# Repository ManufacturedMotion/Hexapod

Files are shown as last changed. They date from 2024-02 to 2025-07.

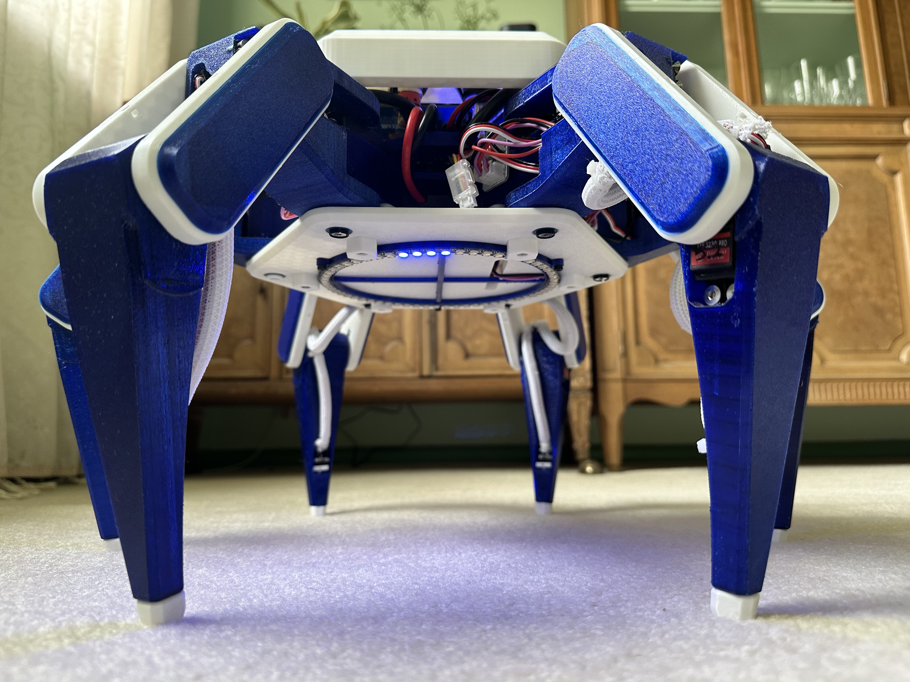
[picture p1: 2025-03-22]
resources/images/Hex2/dillon_bot_1.jpg

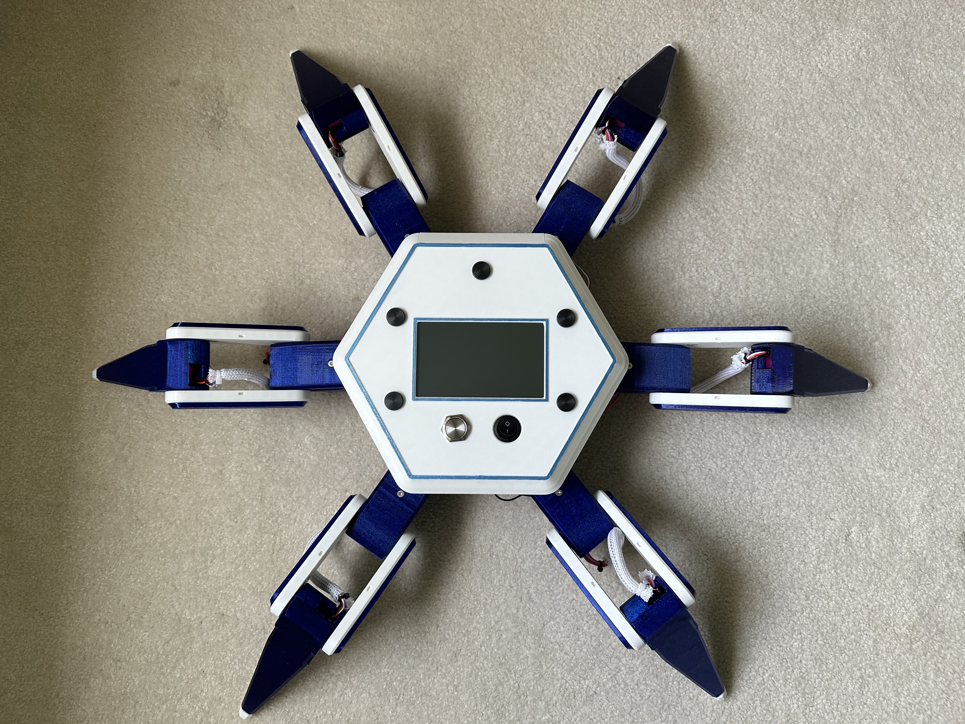
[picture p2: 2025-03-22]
resources/images/Hex2/dillon_bot_5.jpg

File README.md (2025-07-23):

# Hex

Hex is a six legged OpenSource Hexapod designed to serve as a moving platform for you to tinker with and build on top of! We are currently working on the third generation of the platform, Hex3.

If you're interested in learning more about the project, [visit our wiki!](https://github.com/ManufacturedMotion/Hexapod/wiki). If you want to build your own or join the community, check out our [Hex Discord](https://discord.gg/v3bbvRtFUr).

To find out info on what we're planning to change, [checkout our GitHub issues!](https://github.com/ManufacturedMotion/Hexapod/issues).

## Generations

### Hex1

- [Overview](https://github.com/ManufacturedMotion/Hexapod/wiki#mk1)
- Completed: July 2023 - May 2024
- MIT LICENSE

### Hex2
- [Overview](https://github.com/ManufacturedMotion/Hexapod/wiki#mk2)
- Completed: May 2024 - July 2025
- MIT LICENSE

### Hex3
- In-Progress: July 2025 - Present
- GNU GENERAL PUBLIC LICENSE V3

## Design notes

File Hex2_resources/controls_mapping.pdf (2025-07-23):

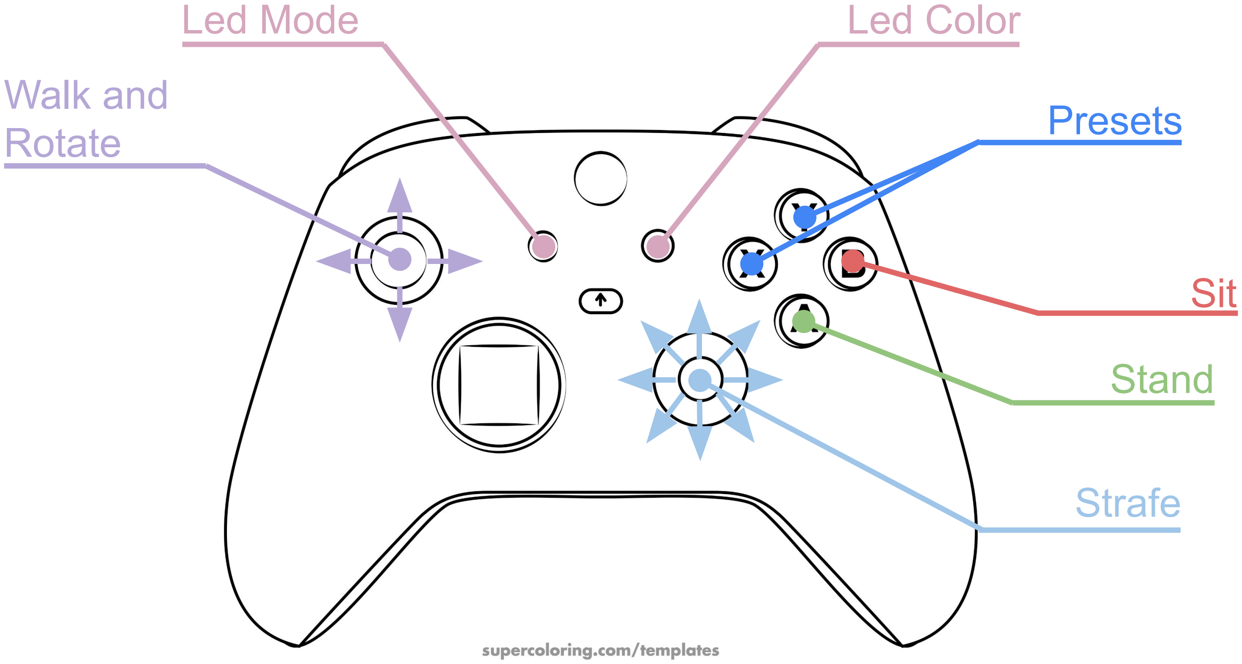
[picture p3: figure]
Walk and Rotate; Strafe; Led Mode; Led Color; Presets; Sit; Stand

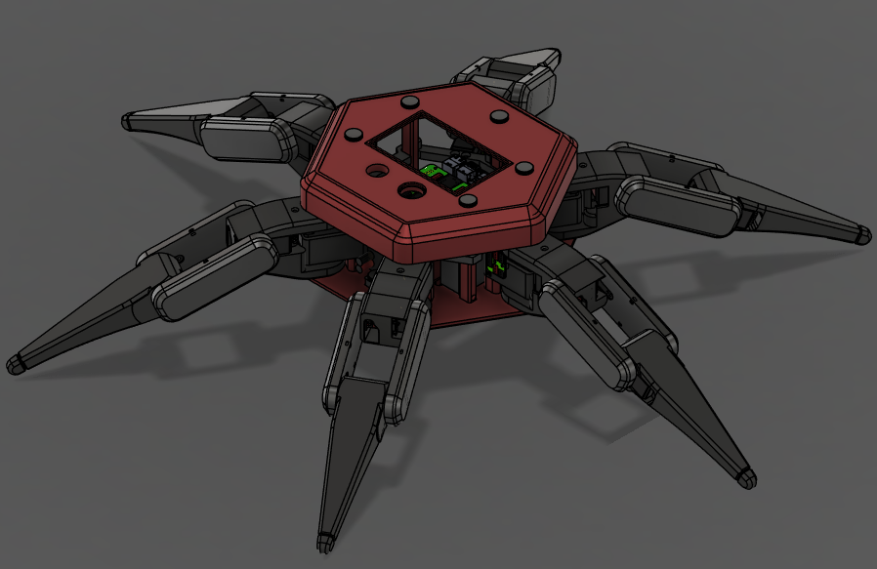
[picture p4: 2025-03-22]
resources/images/Hex2/cad.PNG

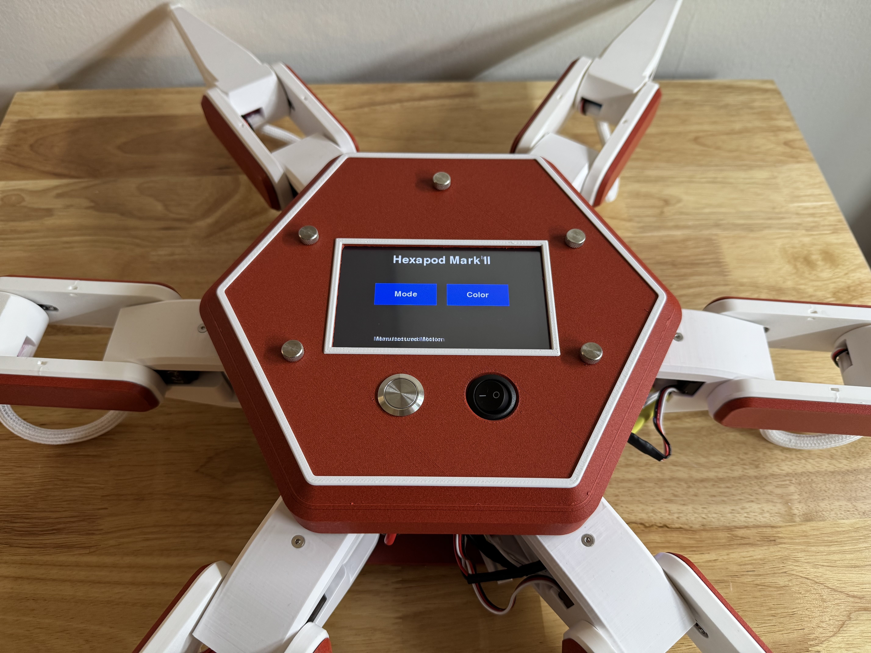
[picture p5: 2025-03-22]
resources/images/Hex2/danny_bot_3.jpg

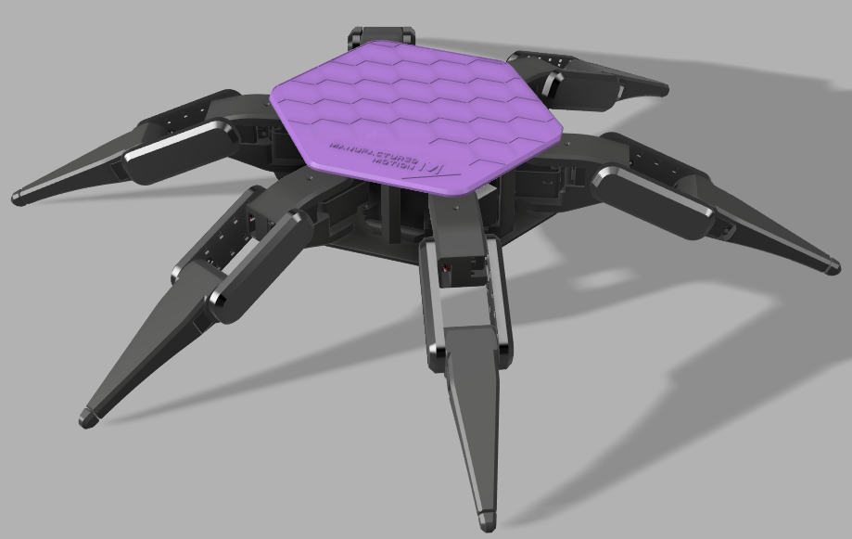
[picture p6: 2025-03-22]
resources/images/Hex1/cad_render.PNG

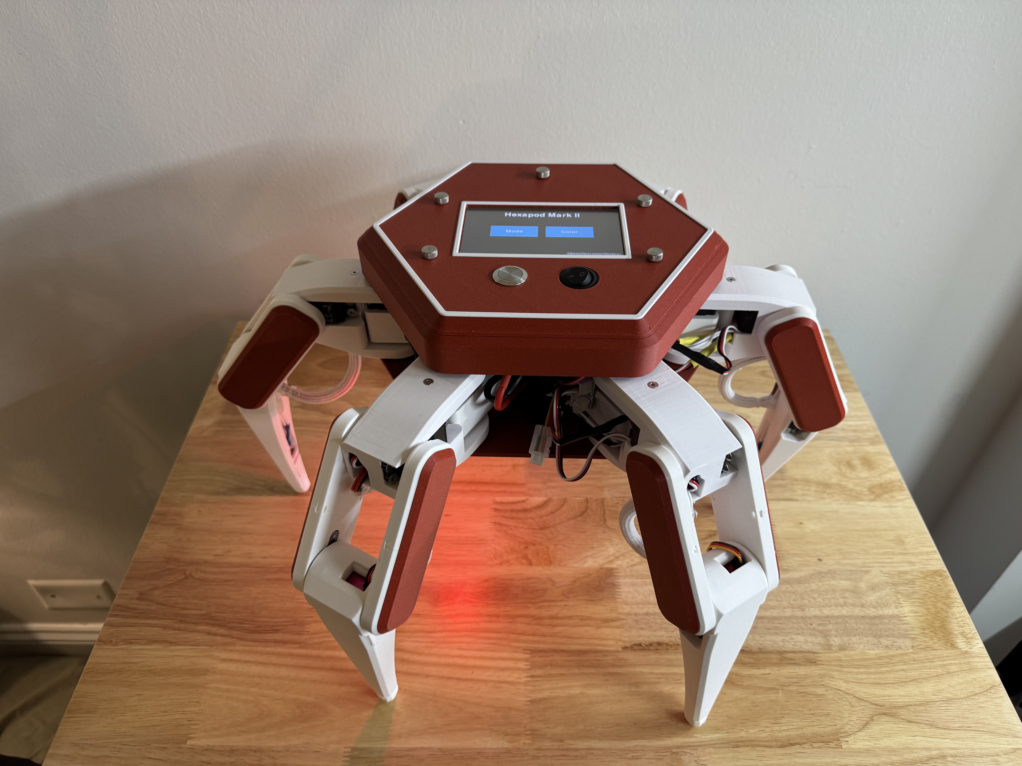
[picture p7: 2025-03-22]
resources/images/Hex2/danny_bot_4.jpg

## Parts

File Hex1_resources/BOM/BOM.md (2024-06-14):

# Bill of Materials

This BOM is non-exhaustive as we pivoted to developing the Hexapod Mk2, which is a more robust platform and solves a lot of the problems found in the Mk1 design. This includes a redesign of most of the 3D printed parts and electronics.

Please use the following parts as guidelines, rather than a definitive list.

## Printed Parts

The following files need to be 3D printed in order to assemble a Hexapod:

| Short Name  | Part Name/Description | Quantity | Notes |
|---|---|---|---|
| Base | Base Piece | 1 | |
| S1 | Segment 1 | 6 | |
| S2 | Segment 2 | 12 | Same part for left and right side |
| S2 Cover | Segment 2 Cover | 12 | Magnetically attached cover for S2 - Decorative Only |
| S3 | Segment 3 | 6 | |
| S3 Switch | Segment 3 Switch Cover | 6 | |
| S3 Mounting | Segment 3 Mounting Extension | 6 | |

Recommended Print Settings:

- 0.2mm layer height
- 3 Vertical Walls
- 10% Triangle Infill

## Electronics

| Category | Part | Quantity |
|---|---|---|
| Electronics | PCB | 1 |
| Electronics | [DS3230Pro-270 Degree Servos](https://www.aliexpress.us/item/2251801756814911.html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) | 18 |
| Electronics | [0805 SMD LED](https://www.amazon.com/dp/B01CUGA8JO/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) | 1 |
| Electronics | [0805 Resistor (Value TBD)](https://www.amazon.com/dp/B08RYMY6XK/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) | 1 |
| Electronics | [SPST Power Switch](https://www.amazon.com/DaierTek-Rocker-Switch-Household-Appliances/dp/B07S1MV462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) | 1 |
| Electronics | [Micro Limit Switch](https://www.amazon.com/dp/B073TYWX86/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) | 6 |
| Electronics | [DC-DC Buck Converter -- 12V to 5V 10A](https://www.amazon.com/dp/B0B1PG4C22/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) | 1 |
| Electronics | [JST-SM](https://www.amazon.com/gp/product/B071HFPXBD/ref=ppx_yo_dt_b_asin_title_o07_s00?ie=UTF8&psc=1) | 18 |
| Electronics | [JST-XH](https://www.amazon.com/gp/product/B07ZK5F8HP/ref=ppx_yo_dt_b_asin_title_o07_s00?ie=UTF8&psc=1) | 6 |
| Electronics | [XT60 PW](https://www.amazon.com/dp/B07VRLQ2C5?psc=1&ref=ppx_yo2ov_dt_b_product_details) | 1 |
| Electronics | [XT30 PW](https://www.amazon.com/dp/B099F2PXYN?psc=1&ref=ppx_yo2ov_dt_b_product_details) | 2 |
| Electronics | [XT30](https://www.amazon.com/dp/B08P5HVMYT?psc=1&ref=ppx_yo2ov_dt_b_product_details) | 2 |
| Electronics | [3s 5200 mAh Battery](https://www.amazon.com/dp/B0972RKJDS/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) | 1 |
| Electronics - Optional | [LiPo Battery Meter](https://www.amazon.com/dp/B0178P8H9U/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) | 1 |
| Electronics | [LiPo Charger](https://www.amazon.com/dp/B00466PKE0/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) | 1 |
| Electronics | [LiPo Charging Bag](https://www.amazon.com/dp/B07KZQZBN2/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) | 1 |
| Electronics | [Bluetooth Gaming Controller](https://www.amazon.com/dp/B0BFQFW9RS/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) | 1 |
| Electronics | [Teensy 4.0](http://d.digikey.com/dc/mn-w0iJh4uEE_bUitNCuXmOASUNxIUHHNt2ANEnMXZ9KmF9gFGcTP6LV0h4vvHht-UX6JWhwD_CEVqRHjYcqVHXxxIfGmGv3GtgizzJ-nkg94oIf-knrnSVyE2xlCqi3eC3-Q9X4k8dmw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) | 1 |
| Electronics | [Raspberry Pi Zero W](https://www.raspberrypi.com/products/raspberry-pi-zero-w/) | 1 |
| Electronics | [20 Awg Silicone Stranded Wire](https://www.amazon.com/dp/B06Y58W228?ref_=cm_sw_r_apin_dp_QD4W8PBN2DN0YP82QZBG&language=en-US&th=1) | TBD |

## Hardware

| Category | Part | Quantity |
|---|---|---|
| Hardware | [M4 x 4.7 Threaded Inserts](https://www.amazon.com/dp/B08T9TXS9S/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) | 72 |
| Hardware | [M3 x 5 Threaded Inserts](https://www.amazon.com/dp/B0CDH36ZMX/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) | 24 |
| Hardware | [6mm x 2mm Magnets](https://www.amazon.com/dp/B0C3B483DV/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) | 48 |
| Hardware | [ID 8mm x OD 14mm x Width 4mm Bearings](https://www.amazon.com/dp/B0C74VQDMM/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) | 12 |
| Hardware | [Hex Drive Flat Head Screw](https://www.mcmaster.com/#92125A190) [M4 x 0.7 mm Thread, 10 mm Long](https://www.mcmaster.com/#92125A190) | 72 |
| Hardware | [Hex Drive Flat Head Screw](https://www.mcmaster.com/#92125A130)[M3 x 0.5 mm Thread, 10 mm Long](https://www.mcmaster.com/#92125A130) | 60 |
| Hardware | [Cup-Point Set Screw](https://www.mcmaster.com/#91390A098)[M3 x 0.5 mm Thread, 4 mm Long](https://www.mcmaster.com/#91390A098) | 6 |
| Hardware | [Dowel Pin](https://www.mcmaster.com/#91585A573)[5 mm Diameter, 40 mm Long](https://www.mcmaster.com/#91585A573) | 6 |
| Hardware | [M2x10 Self Tap Screws](https://a.co/d/agRSm9J) | 12 |

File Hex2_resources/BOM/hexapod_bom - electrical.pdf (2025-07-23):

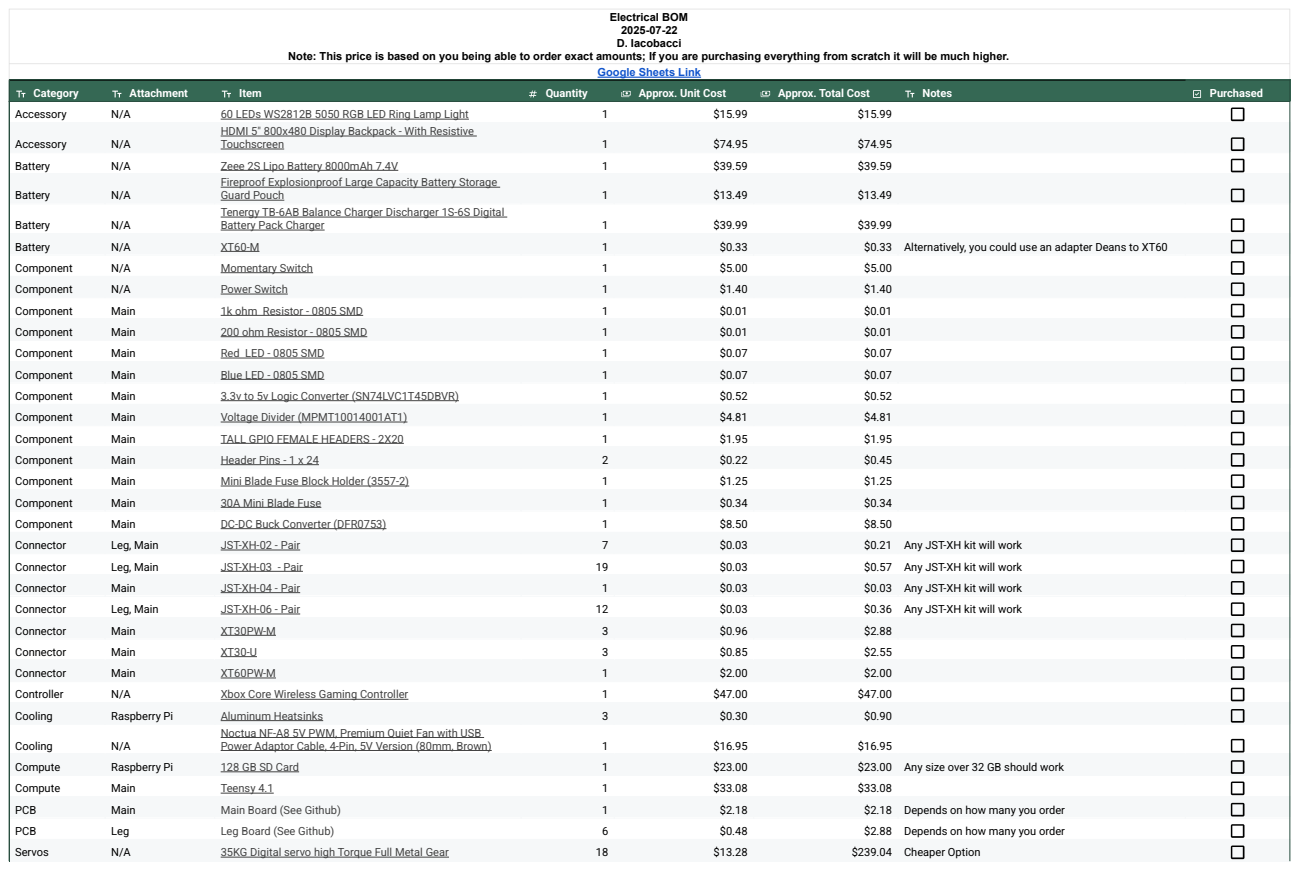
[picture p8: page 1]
Electrical BOM 2025-07-22 D. Iacobacci

Note: This price is based on you being able to order exact amounts; If you are purchasing everything from scratch it will be much higher.

Google Sheets Link (https://docs.google.com/spreadsheets/d/1nSNH1yMX1RCnKzeOJ6oc8cjoijGXfABLivroaHwzo4E/edit?usp=sharing)

Category | Attachment | Item | Quantity | Approx. Unit Cost | Approx. Total Cost | Notes | Purchased
Accessory | N/A | 60 LEDs WS2812B 5050 RGB LED Ring Lamp Light (https://www.amazon.com/dp/B083W2ZWTQ?ref_=ppx_hzsearch_conn_dt_b_fed_asin_title_1&th=1) | 1 | $15.99 | $15.99
Accessory | N/A | HDMI 5" 800x480 Display Backpack - With Resistive Touchscreen (https://www.adafruit.com/product/2260) | 1 | $74.95 | $74.95

Battery | N/A | Zeee 2S Lipo Battery 8000mAh 7.4V (https://www.amazon.com/dp/B073S2W6PZ/?coliid=I2N19MYR3S8E68&colid=2MOGJRAIUFLT0) | 1 | $39.59 | $39.59
Battery | N/A | Fireproof Explosionproof Large Capacity Battery Storage Guard Pouch (https://a.co/d/0e39bDe3) | 1 | $13.49 | $13.49

Battery | N/A | Tenergy TB-6AB Balance Charger Discharger 1S-6S Digital Battery Pack Charger (https://a.co/d/04OFANOm) | 1 | $39.99 | $39.99

Battery | N/A | XT60-M (https://www.amazon.com/dp/B07VRZR5TL?ref_=ppx_hzsearch_conn_dt_b_fed_asin_title_2) | 1 | $0.33 | $0.33 | Alternatively, you could use an adapter Deans to XT60

Component | N/A | Momentary Switch (https://a.co/d/0b9twNSM) | 1 | $5.00 | $5.00

Component | N/A | Power Switch (https://a.co/d/0cDl28JW) | 1 | $1.40 | $1.40

Component | Main | 1k ohm Resistor - 0805 SMD (https://a.co/d/05essy1o) | 1 | $0.01 | $0.01

Component | Main | 200 ohm Resistor - 0805 SMD (https://a.co/d/05essy1o) | 1 | $0.01 | $0.01

Component | Main | Red LED - 0805 SMD | 1 | $0.07 | $0.07

Component | Main | Blue LED - 0805 SMD (https://a.co/d/07H2SZfK) | 1 | $0.07 | $0.07

Component | Main | 3.3v to 5v Logic Converter (SN74LVC1T45DBVR) (https://www.digikey.com/en/products/detail/texas-instruments/SN74LVC1T45DBVR/639455) | 1 | $0.52 | $0.52

Component | Main | Voltage Divider (MPMT10014001AT1) (https://www.digikey.com/en/products/detail/vishay-dale-thin-film/MPMT10014001AT1/1771066) | 1 | $4.81 | $4.81

Component | Main | TALL GPIO FEMALE HEADERS - 2X20 (https://www.digikey.com/en/products/detail/sparkfun-electronics/PRT-21570/18635154) | 1 | $1.95 | $1.95

Component | Main | Header Pins - 1 x 24 (https://www.amazon.com/dp/B0CTKF2NC6/?coliid=I3O1AXN49NW8LT&colid=2MOGJRAIUFLT0) | 2 | $0.22 | $0.45

Component | Main | Mini Blade Fuse Block Holder (3557-2) (https://www.digikey.com/en/products/detail/keystone-electronics/3557-2/2137305) | 1 | $1.25 | $1.25

Component | Main | 30A Mini Blade Fuse (https://www.digikey.com/en/products/detail/littelfuse-inc/0891030-NXWS/5233823) | 1 | $0.34 | $0.34

Component | Main | DC-DC Buck Converter (DFR0753) (https://www.digikey.com/en/products/detail/dfrobot/DFR0753/13590872) | 1 | $8.50 | $8.50

Connector | Leg, Main | JST-XH-02 - Pair (https://a.co/d/03VvZ2aq) | 7 | $0.03 | $0.21 | Any JST-XH kit will work

Connector | Leg, Main | JST-XH-03 - Pair (https://a.co/d/03VvZ2aq) | 19 | $0.03 | $0.57 | Any JST-XH kit will work

Connector | Main | JST-XH-04 - Pair (https://a.co/d/03VvZ2aq) | 1 | $0.03 | $0.03 | Any JST-XH kit will work

Connector | Leg, Main | JST-XH-06 - Pair (https://a.co/d/03VvZ2aq) | 12 | $0.03 | $0.36 | Any JST-XH kit will work

Connector | Main | XT30PW-M (https://a.co/d/0aSlfwzo) | 3 | $0.96 | $2.88

Connector | Main | XT30-U (https://a.co/d/017gKTzp) | 3 | $0.85 | $2.55

Connector | Main | XT60PW-M (https://a.co/d/06amuL7W) | 1 | $2.00 | $2.00

Controller | N/A | Xbox Core Wireless Gaming Controller (https://a.co/d/02mnp9V5) | 1 | $47.00 | $47.00

Cooling | Raspberry Pi | Aluminum Heatsinks (https://a.co/d/04IbYiWU) | 3 | $0.30 | $0.90
Cooling | N/A | Noctua NF-A8 5V PWM, Premium Quiet Fan with USB Power Adaptor Cable, 4-Pin, 5V Version (80mm, Brown) (https://a.co/d/0ccSLfRo) | 1 | $16.95 | $16.95

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

Electrical BOM
2025-07-22
D. Iacobacci
Note: This price is based on you being able to order exact amounts; If you are purchasing everything from scratch it will be much higher. Google Sheets Link (https://docs.google.com/spreadsheets/d/1nSNH1yMX1RCnKzeOJ6oc8cjoijGXfABLivroaHwzo4E/edit?usp=sharing)
Category | Attachment | Item | Quantity | Approx. Unit Cost | Approx. Total Cost | Notes | Purchased
Servos | N/A | GoBilda 2000 Series Dual Mode Servo (25-2, Torque) | 18 | $31.44 | $565.92 | Price includes 15% bulk discount if you order 20 or more -- email GoBilda directly.
Compute | Raspberry Pi | Raspberry Pi 5 - 8 GB RAM (https://www.adafruit.com/product/5813) | 1 | $80.00 | $80.00
Wiring | N/A | Micro HDMI to HDMI Wire A2-D2 (https://www.aliexpress.us/item/3256802017399860.html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) | 0 | $2.35 | $0.00 | Confirm orientation works for your screen and pi
Wiring | N/A | Main to Leg Connections <TBD> | 0 | $ -
Wiring | N/A | 12 Gauge Wire (https://www.amazon.com/dp/B07CZZ11K2/?coliid=I1EO3TKVNQHO26&colid=2MOGJRAIUFLT0) | 1 | $0.66 | $0.66 | Used for the power switch as it has the full battery current; Could likely go with a lower gauge
| | | | $0.66 | $0.00
| | | | $0.66 | $0.00
| | | | | $663.01 | Price with AliExpress servos
| | | | | $989.89 | Price with GoBilda servos

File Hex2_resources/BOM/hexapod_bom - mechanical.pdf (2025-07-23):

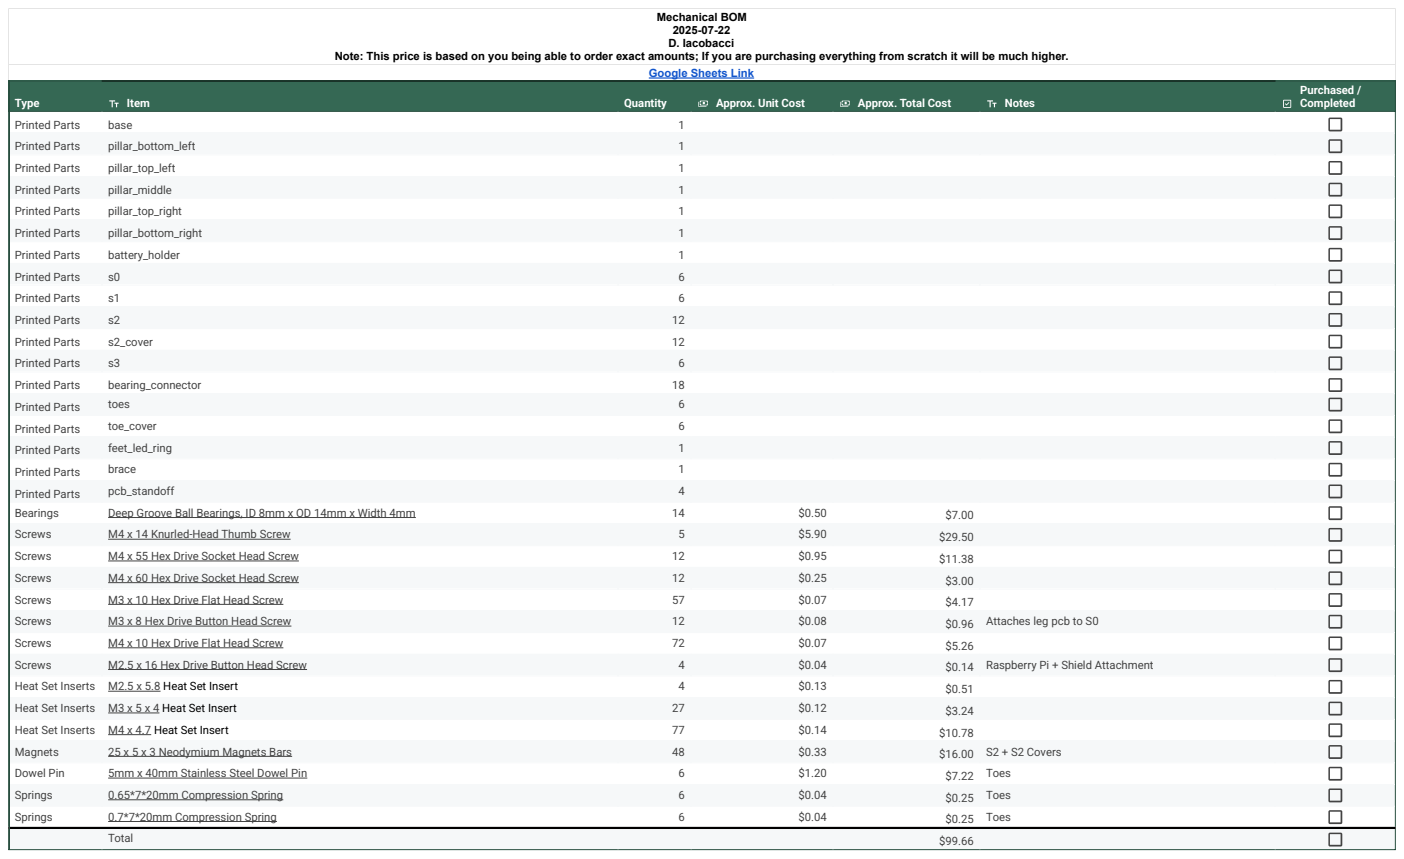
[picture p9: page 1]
Mechanical BOM 2025-07-22 D. Iacobacci

Note: This price is based on you being able to order exact amounts; If you are purchasing everything from scratch it will be much higher.

Google Sheets Link (https://docs.google.com/spreadsheets/d/1nSNH1yMX1RCnKzeOJ6oc8cjoijGXfABLivroaHwzo4E/edit?usp=sharing)

Type | Item | Quantity | Approx. Unit Cost | Approx. Total Cost | Notes | Purchased / Completed

Printed Parts | base | 1

Printed Parts | pillar_bottom_left | 1

Printed Parts | pillar_top_left | 1

Printed Parts | pillar_middle | 1

Printed Parts | pillar_top_right | 1

Printed Parts | pillar_bottom_right | 1

Printed Parts | battery_holder | 1

Printed Parts | s0 | 6

Printed Parts | s1 | 6

Printed Parts | s2 | 12

Printed Parts | s2_cover | 12

Printed Parts | s3 | 6

Printed Parts | bearing_connector | 18
Printed Parts | toes | 6

Printed Parts | toe_cover | 6

Printed Parts | feet_led_ring | 1

Printed Parts | brace | 1

Printed Parts | pcb_standoff | 4

Bearings | Deep Groove Ball Bearings, ID 8mm x OD 14mm x Width 4mm (https://www.amazon.com/gp/product/B0C74VQDMM/ref=ppx_yo_dt_b_search_asin_title?ie=UTF8&th=1) | 14 | $0.50 | $7.00

Screws | M4 x 14 Knurled-Head Thumb Screw (https://www.mcmaster.com/92545a155/) | 5 | $5.90 | $29.50

Screws | M4 x 55 Hex Drive Socket Head Screw (https://www.mcmaster.com/catalog/91292A268) | 12 | $0.95 | $11.38

Screws | M4 x 60 Hex Drive Socket Head Screw | 12 | $0.25 | $3.00

Screws | M3 x 10 Hex Drive Flat Head Screw (https://www.mcmaster.com/catalog/92125A130) | 57 | $0.07 | $4.17

Screws | M3 x 8 Hex Drive Button Head Screw (https://www.mcmaster.com/92095A181) | 12 | $0.08 | $0.96 | Attaches leg pcb to S0

Screws | M4 x 10 Hex Drive Flat Head Screw (https://www.mcmaster.com/92125A130/) | 72 | $0.07 | $5.26

Screws | M2.5 x 16 Hex Drive Button Head Screw (https://www.amazon.com/gp/product/B09CPDVYB7/ref=ppx_yo_dt_b_search_asin_title?ie=UTF8&psc=1) | 4 | $0.04 | $0.14 | Raspberry Pi + Shield Attachment

Heat Set Inserts | M2.5 x 5.8 Heat Set Insert | 4 | $0.13 | $0.51

Heat Set Inserts | M3 x 5 x 4 Heat Set Insert | 27 | $0.12 | $3.24

Heat Set Inserts | M4 x 4.7 Heat Set Insert | 77 | $0.14 | $10.78

Magnets | 25 x 5 x 3 Neodymium Magnets Bars (https://www.amazon.com/gp/product/B09YCWKBMP/ref=ppx_yo_dt_b_search_asin_title?ie=UTF8&th=1) | 48 | $0.33 | $16.00 | S2 + S2 Covers

Dowel Pin | 5mm x 40mm Stainless Steel Dowel Pin (https://www.mcmaster.com/91585A573/) | 6 | $1.20 | $7.22 | Toes

Springs | 0.65*7*20mm Compression Spring (https://www.amazon.com/dp/B0BBQL2SN3?ref_=ppx_hzsearch_conn_dt_b_fed_asin_title_3) | 6 | $0.04 | $0.25 | Toes

Springs | 0.7*7*20mm Compression Spring (https://www.amazon.com/dp/B0BBQL2SN3?ref_=ppx_hzsearch_conn_dt_b_fed_asin_title_3) | 6 | $0.04 | $0.25 | Toes

Total | | | $99.66

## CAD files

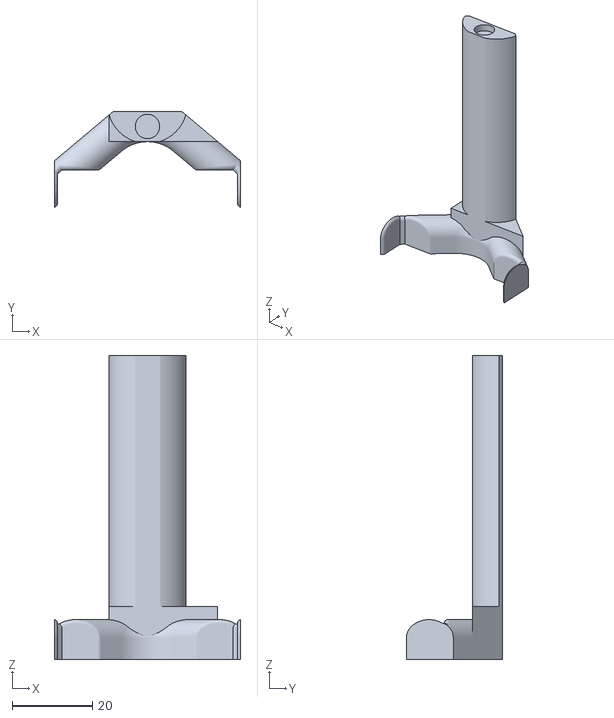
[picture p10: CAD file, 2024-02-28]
Hex1_resources/CAD/base_batteryholder_final.stl
46.5 x 24.0 x 76.0

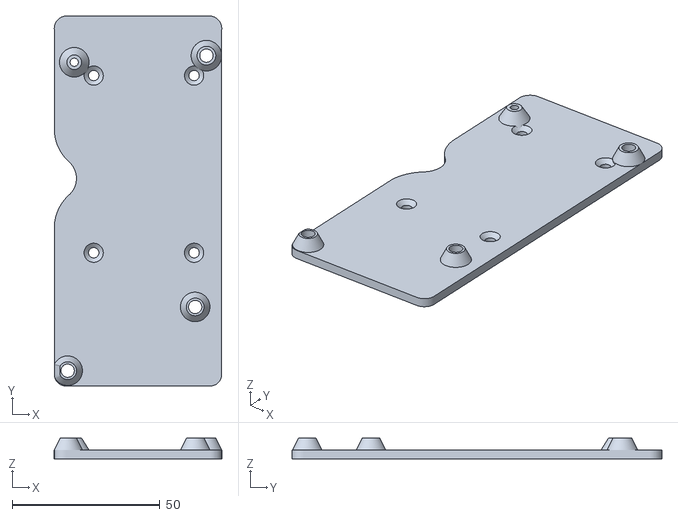
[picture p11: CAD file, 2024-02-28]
Hex1_resources/CAD/pcb_mount_final.stl
56.7 x 125.3 x 7.00

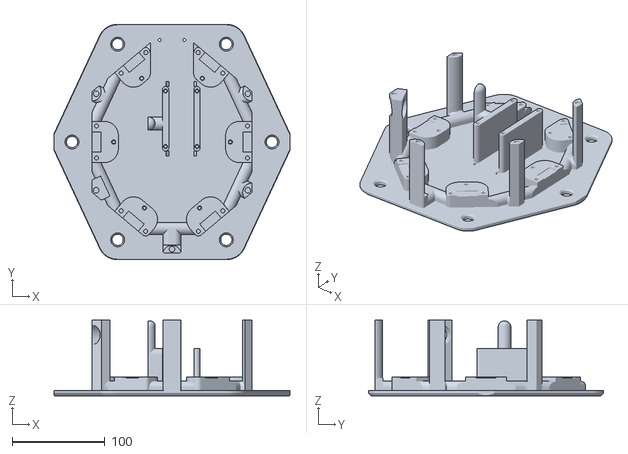
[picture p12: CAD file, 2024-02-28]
Hex1_resources/CAD/base_bottom_final.stl
255.0 x 254.4 x 82.0

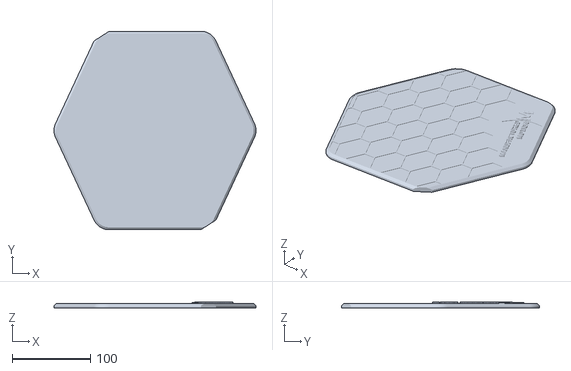
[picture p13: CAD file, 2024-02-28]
Hex1_resources/CAD/lid_wlogo_final.stl
259.0 x 254.4 x 8.00

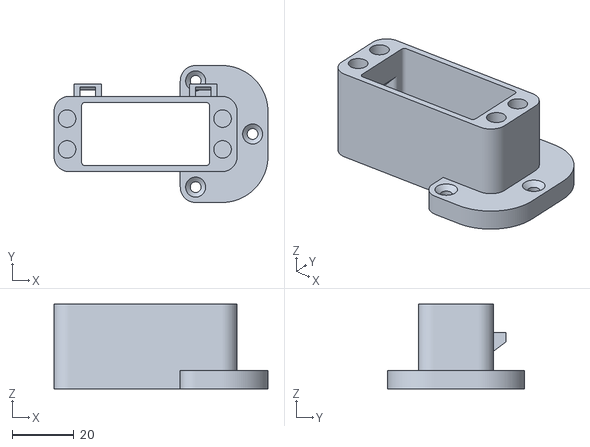
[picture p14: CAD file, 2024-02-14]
Hex1_resources/CAD/L2,3,4,5 - S1 Motor Mount - Final.stl
69.5 x 44.5 x 27.5

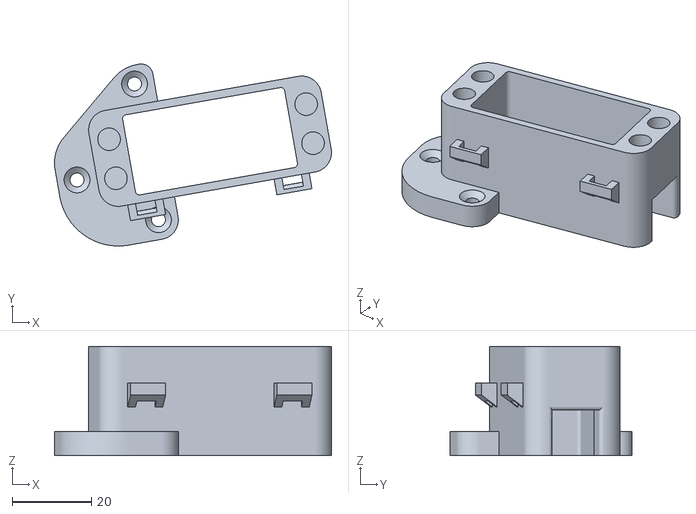
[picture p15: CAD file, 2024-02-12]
Hex1_resources/CAD/L2 - S1 Motor Mount - Final.stl
69.9 x 45.9 x 27.5

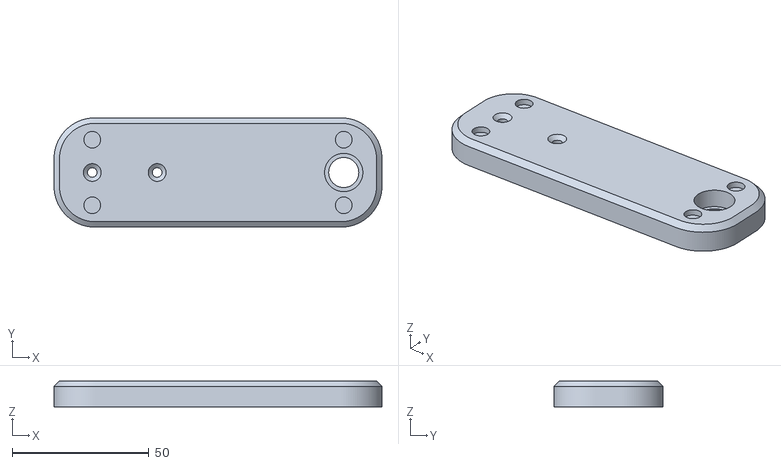
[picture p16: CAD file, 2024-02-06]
Hex1_resources/CAD/S2 Final.stl
120.0 x 40.0 x 9.50

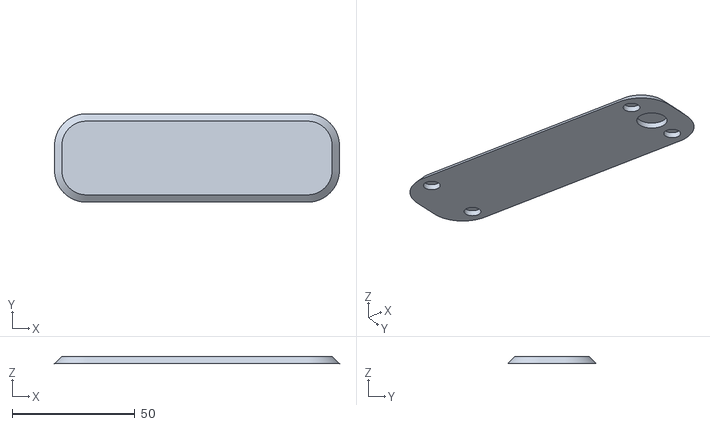
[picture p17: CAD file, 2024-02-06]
Hex1_resources/CAD/S2 Cover Final.stl
116.0 x 36.0 x 3.00

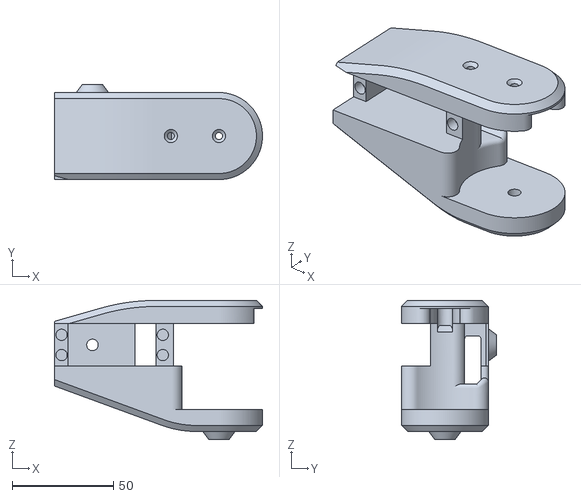
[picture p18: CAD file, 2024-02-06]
Hex1_resources/CAD/S1 Final.stl
102.8 x 47.0 x 68.8

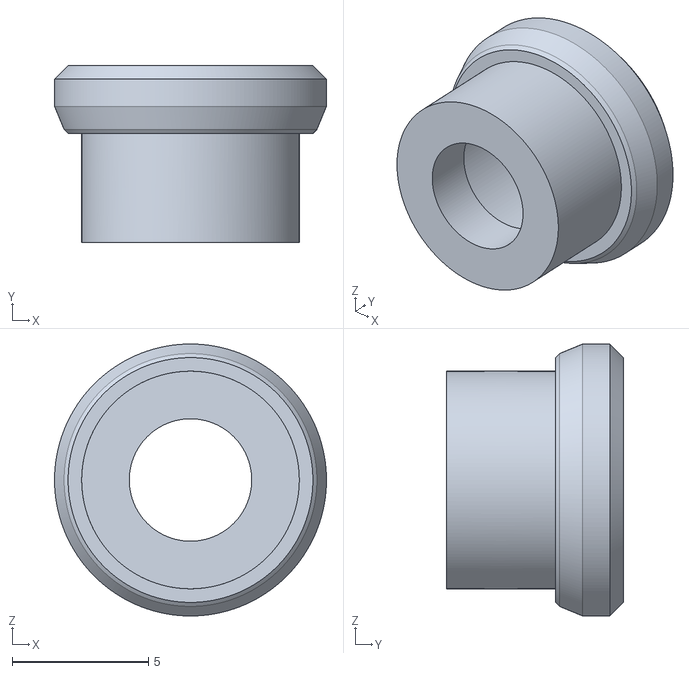
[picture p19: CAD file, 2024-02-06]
Hex1_resources/CAD/Bearing Holder.stl
10.0 x 6.50 x 10.00

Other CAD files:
Hex1_resources/CAD/L6 - S1 Motor Mount - Final.stl

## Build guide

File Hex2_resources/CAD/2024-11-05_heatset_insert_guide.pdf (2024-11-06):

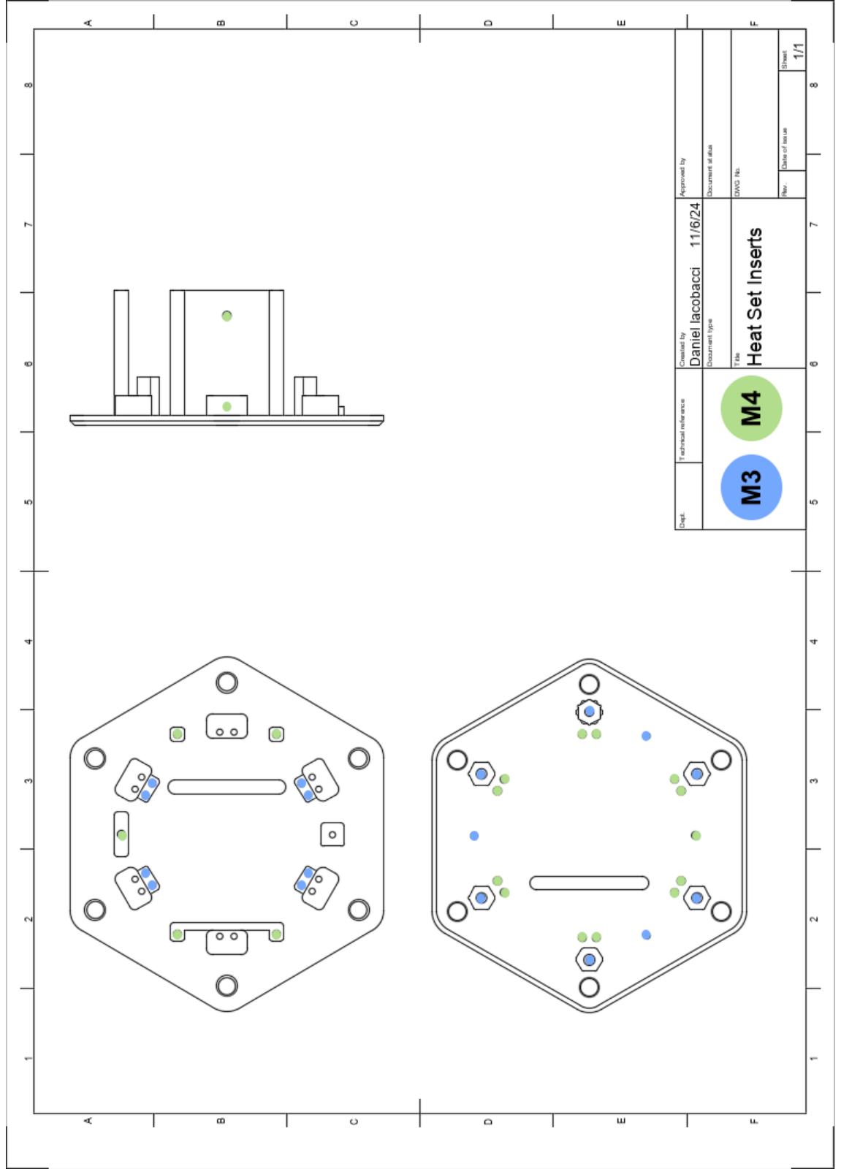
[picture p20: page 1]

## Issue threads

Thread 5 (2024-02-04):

Header File with Configuration

Diacoba1, 2024-02-04:
Write code that takes in an offsets.h file and can use each of our offsets in the code. Should be flexible enough that we just need to specify whose bot it is, and the rest is abstracted away.

DillonKane, 2024-02-05:
First rev done. Could not dynamically create an array of axis objects and then use a for loop to define motor pins, etc. Instead that is hard coded for now -- this was what I was trying:

```
Axis axes[6][3];
  for (uint8_t i = 0; i < 6; i++) {
    for (uint8_t j = 0; j < 3; j++) {
        axes[i][j] = Axis(pwm_pins[i][j], min_pos[i][j] * scale_fact[i][j], max_pos[i][j] * scale_fact[i][j]);
    }
  }
```
This was not correctly meshing with the servos

Diacoba1, 2024-02-29:
- [ ] PWM pins defined per user
- [ ] Swap zero points for L1 & L2 for Danny and Zack
- [ ] Move `#define USER DILLON` to before the includes of the Arduino file

DillonKane, 2024-02-29:
https://github.com/ManufacturedMotion/HexapodController/pull/2

Closed 2024-02-29.

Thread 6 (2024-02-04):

Update the Base to allow for Battery removal

Diacoba1, 2024-02-04:
Modify the base to allow the battery to be slid in and out on the side with the custom fit brackets. It should be held in place with the lid mounting piece that has two screws.

Diacoba1, 2024-02-06:
#10

Closed 2024-02-06.

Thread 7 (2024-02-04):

Update the S1 Mounting

Diacoba1, 2024-02-04:
Update the S1 Mounting to:

- Allow for 4 screws to be used
- Have the chamfer on the correct side
- Have the mounting screws in the correct place

Closed 2024-02-12.

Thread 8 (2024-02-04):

Position and Orientation of Robot

Diacoba1, 2024-02-04:
From ChatGPT:
I have a robot with three legs. With it standing on those three legs, I want it to calculate the position and orientation of the center of the robot. How can I do this?

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

Diacoba1, 2024-02-29:
Decided coordinate system, in progress. Need to figure out how Yaw impacts X and Y

Closed 2024-04-04.

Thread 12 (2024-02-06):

Update Servo Mounts

DillonKane, 2024-02-06:
update screw spacing on all servo mounts so all 4 screws can be used

Diacoba1, 2024-02-12:
Cleared assignees -- we should only assign to one person so we know who is tackling it

Diacoba1, 2024-02-12:
I have already updated S1, and S2. The final change needs to be done for S3. But we should lump it in with the toe fixes

Diacoba1, 2024-02-13:
- [ ] Update S1 Motor mount to not have an overhang
- [ ] Check out S3 spacing

Closed 2024-02-14.

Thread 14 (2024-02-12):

Update S3 Toe Mount

Diacoba1, 2024-02-12:
Update S3 so the toe rod is held in place, and the limit switch cover so we don't need to cut away parts of S3

Diacoba1, 2024-03-15:
Dillon test this

Closed 2024-03-28.

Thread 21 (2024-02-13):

Raspberry Pi Passthrough

Diacoba1, 2024-02-13:
- [ ] A pass through using serial to send commands to the Teensy
- [ ] SSH into the raspberry pi wirelessly, run a script that gives us a serial monitor

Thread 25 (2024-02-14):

Design the Lid

Diacoba1, 2024-02-14:
The lid should meet the following requirements:

- [x] Be able to be printed in two colors without the need of an AMS
- [x] Have the Manufactured Motion Logo Printed on the Lid
- [x] Securely attach to the base with as few screws as possible (max 6)
- [x] Attach with screws standard to the rest of the bot
- [x] Provide access to the switch
- [x] Cover cables without significantly increasing height or restricting range of motion

Closed 2024-02-28.

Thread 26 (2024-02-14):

Redesign S3

Diacoba1, 2024-02-14:
Redesign S3 to address the following issues/concerns:

- [x] The zip tie mounts in the cable channel do not function properly
- [x] The servo can only use 2/4 screws
- [x] The motor connector piece can easily be overtightened, cracking the piece
- [x] The part is not optimized for 3D printing -- significant supports are needed and they are hard to remove

Diacoba1, 2024-04-03:
Just need to upload the new files to Github

Closed 2024-04-14.

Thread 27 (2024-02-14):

PCB Second Generation

Diacoba1, 2024-02-14:
Making this issue to track future improvements to the PCB:

- [x] **Convert the PCB to working with a Raspberry Pi 5 instead of a Pi Zero W**
- [x] PCB should attach to the Raspberry Pi (breakout attachment)
- [x] Change the motor connector order so it goes 123 instead of 213
- [x] Change the switch connector to be an XT-30 instead of two vias
- [x] Improve the readability of the silkscreen once connectors are attached
- [x] ~Add in physical low voltage cutoff~ Dropping this in favor of a way to read the voltage and get those values on the pi.
- [x] ~Add in Touchscreen for current status~ USB + HDMI, no physical connections required
- [x] Lever to switch between control modes (redesign not required) (Or dipswitches on the board?)
- [x] ~Big button for regular and autonomous~ Deprecating in favor of the touch screen
- [x] ~1-3 LEDs for status indication~ Deprecating in favor of the touch screen
- [x] Add in the Manufactured Motion logo to the back of the PCB
- [x] ~Connections for Lidar~ -- should be USB

Diacoba1, 2024-06-04:
#83 Began working on some of these points

Diacoba1, 2024-06-25:
#97

Closed 2024-06-25.

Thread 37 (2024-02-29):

Measure from actual center of bot to S1 for each leg

Diacoba1, 2024-02-29:
Measure from actual center of bot to S1 for each leg. Get the X and Y offsets.

- With battery on the bottom, L/R is X, Up/Down is Y.
- Half the values should be negative

3 | 4
2 | 5
1 | 6

Diacoba1, 2024-03-09:
#45

Closed 2024-03-09.

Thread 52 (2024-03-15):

Update Example File

Diacoba1, 2024-03-15:
- [x] Case 0 is a break
- [x] Case 1-6 controls that specific legs IK
- [x] Case 7 move to all zeros
- [x] Each case should have its own scanf

Diacoba1, 2024-03-23:
https://github.com/ManufacturedMotion/HexapodController/pull/4

Closed 2024-03-23.

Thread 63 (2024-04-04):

WebServer Enhancements

Diacoba1, 2024-04-04:
- [x] Swap from Threads to multiprocessing (true multi-threading) on the Pi
- [x] Fix the read serial action so it is properly sent to the webpage

Diacoba1, 2024-04-04:
#65

Closed 2024-04-04.

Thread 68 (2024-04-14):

Raspberry Pi as a WAP

Diacoba1, 2024-04-14:
- [x] If there is a network available, use that network
- [x] If there is not, launch a soft-access point

Diacoba1, 2024-06-21:
A lot of these issues go away with the transition to a full pi running Ubuntu, so closing out

Closed 2024-06-21.

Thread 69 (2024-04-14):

Raspberry Pi WebServer does not function w/o hard access point

Diacoba1, 2024-04-14:
- [ ] Flask WebServer fails without an internet connection -- why?
- [ ] Logo is not rendered as it is hosted on Github

Diacoba1, 2024-06-25:
Not an issue with running Ubuntu, we can have it act as a bridge between the network and the user

Closed 2024-06-25.

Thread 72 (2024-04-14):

Leg Breakout Boards

Diacoba1, 2024-04-14:
Instead of needing each leg to have a wiring harness, we should design a small PCB to mount to each S0.

- [x] Connectors for the data for each servo
- [x] Common ground and 5v lines
- [x] Screw mounting

Diacoba1, 2024-06-21:
#88

Closed 2024-06-21.

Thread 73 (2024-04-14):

Hexapod Gen 2

Iacobacci, 2024-04-14:
- [x] **Redesign the hexapod base to function with the Gen 2 PCB**
- [x] Significantly larger magnets so the base could be lifted up from the magnets
- [x] Adjust the logo on the lid so it always is at the back of the hexapod
- [x] Modify S1 to be able to fit connectors through the cable routing hole

Iacobacci, 2024-08-22:
#107

Closed 2024-08-22.

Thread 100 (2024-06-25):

Test the mk2 main board

Iacobacci, 2024-06-25:
Confirm the following works:

- [x] Voltage divider outputs a voltage within the acceptable range for the pins
- [x] pi can control LED ring
- [x] pi can talk to teensy
- [x] pi can control fan
- [x] voltage divider sends correct value to teensy (battery reading)
- [x] new board can control servos

DillonKane, 2024-08-24:
can measure temp for fan control logic with "sudo vcgencmd measure_temp"

DillonKane, 2024-08-24:
voltage divider needs to be multiplied by offset of 0.01606 to get correct reading

DillonKane, 2024-08-31:
voltage divider sends vdd of 2.45 with battery vdd of 12.3V

zschwid, 2024-10-13:
Can we get a status update here?

DillonKane, 2024-11-19:
Pi can control LED ring if jumper connector is used for LED signal wire. Jumper connects SIG to Pi pin MOSI SCLK0.

Will be addressed with PCB redesign

Closed 2024-11-19.

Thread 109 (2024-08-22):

"Final" CAD Revisions

Iacobacci, 2024-08-22:
- [x] Update S2 Magnets
- [x] S3 Revisions
- [x] Modify lid to cover bot more
- [x] Expand buffer around battery
- [x] Tighter tolerance on brace
- [x] Chamfer brace corners
- [x] Make middle lid support wider
- [x] Cable management

Iacobacci, 2024-08-27:
#111

Closed 2024-08-27.

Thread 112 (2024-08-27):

Mechanical BOM

Iacobacci, 2024-08-27:
Put together a BOM of all the mechanical parts (3D printed parts, screws, bearings, magnets, etc) needed to assemble the hexapod

Iacobacci, 2025-01-20:
Rough draft done in #152 , closing out until project is complete

Closed 2025-01-20.

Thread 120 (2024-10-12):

Assess walking robot simulation frameworks

zschwid, 2024-10-12:
Determine a good framework to use for simulation of the hexapod for RL training

Iacobacci, 2025-02-14:
Switching from Gazebo to IsaacGym

Closed 2025-02-14.

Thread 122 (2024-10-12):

Model has inconsistencies with small motions

zschwid, 2024-10-12:
Very small steps can lead to commanding positions that the hexapod mechanically cannot keep up with. Rework model to account for this case

Closed 2025-02-14.

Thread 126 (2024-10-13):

Voltage drops momentarily when all motors make collision, causing the RPi to shutdown due to undervoltage

zschwid, 2024-10-13:
Fixes to try:
- Add bulk / decoupling capacitance
- Bigger buck converter

Iacobacci, 2024-11-14:
We are going to remediate this with a PCB re-design to run the servos independently off the battery, with the Buck converter being dedicated to the Pi, Fan, LEDs, and other peripherals. Tracked In #130

Closed 2024-11-14.

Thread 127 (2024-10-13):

CAD Changes

zschwid, 2024-10-13:
- [x] S0 PCB mounting
- [x] Bracket (Brace)
- [x] Lid fixes
- [x] Upload archive to git

Closed 2024-11-06.

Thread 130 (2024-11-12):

PCB Redesign

Iacobacci, 2024-11-12:
Redesign the PCB to isolate the servo power and the 5V regulated power.

Schematic:
- [x] Validate the servos can run directly off a 7.4v battery (and up to the maximum charge).
- [x] Run the servos off 7.4v (battery voltage) rather than 5v from the buck converter.
- [x] Add a replaceable fuse (40A) off the battery as a maximum draw.
- [x] ~Switch the Dip Switch to be through hole rather than surface mount.~ Remove the dip switches
- [x] Update Pi power switch to use Pins 9 and 11 (GND, GPIO 17)

Board:
- [x] New board layout
- [x] Order board via JLC/PCBway

Closed 2024-11-26.

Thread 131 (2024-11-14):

Raspberry Pi Soft Shutdown

Iacobacci, 2024-11-14:
The raspberry pi should trigger a soft shutdown when the appropriate button is pressed. This will prevent the SD card from corrupting, which is caused by improper shutdowns.

Closed 2024-11-24.

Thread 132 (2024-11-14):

Xbox Controller to Single Leg Control

Iacobacci, 2024-11-14:
To test the integration of the system, limited by the Hexapod's power distribution, I think we should prioritize testing with one leg and the Xbox Controller.

Test would require:

- [x] Controller to sync correctly to the Pi
- [x] A script on the pi to parse controller inputs
- [x] The pi to send those commands over serial
- [x] The Teensy to be able to process those commands
- [x] The teensy to issue instructions to the leg.

We have most of these pieces functioning independently, but they are not fully functioning together.

DillonKane, 2025-03-02:
Done as per: https://github.com/ManufacturedMotion/Hexapod/pull/186 which allows controller to send preset commands or walk instructions over serial

Closed 2025-03-02.

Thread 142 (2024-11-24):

Test PCB Rev 2.0

Iacobacci, 2024-11-24:
Test:

- [x] Confirm buck converter voltage
- [x] Confirm all 18 servos could function without platform instability
- [x] Test Pi Powerswitch
- [x] LED functionality

Closed 2024-12-28.

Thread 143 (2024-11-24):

Increase S0/S1 Wire Clearance

Iacobacci, 2024-11-24:
- Increase clearance for wires for S0/S1 so the cables no longer get caught

Closed 2024-12-29.

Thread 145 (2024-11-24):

Dead Code Cleanup

Iacobacci, 2024-11-24:
Ensure deprecated code is removed. Necessary after the Fall Surge

DillonKane, 2025-01-13:
I think we caught a lot of this during the first pass, but here is what I found this time around.

Undefined functions:

- [hexapod.hpp firstStepSetup](https://github.com/ManufacturedMotion/Hexapod/blob/main/mk2/code/real_time/teensy_code/lib/HexapodController/src/hexapod.hpp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)
- [leg.hpp linearMove](https://github.com/ManufacturedMotion/Hexapod/blob/main/mk2/code/real_time/teensy_code/lib/HexapodController/src/leg.hpp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)
- [leg.hpp runLegSpeed](https://github.com/ManufacturedMotion/Hexapod/blob/main/mk2/code/real_time/teensy_code/lib/HexapodController/src/leg.hpp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)
- [leg.hpp setLeg](https://github.com/ManufacturedMotion/Hexapod/blob/main/mk2/code/real_time/teensy_code/lib/HexapodController/src/leg.hpp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)
- [leg.hpp _linearMovement](https://github.com/ManufacturedMotion/Hexapod/blob/main/mk2/code/real_time/teensy_code/lib/HexapodController/src/leg.hpp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)
- [position.hpp addPos](https://github.com/ManufacturedMotion/Hexapod/blob/main/mk2/code/real_time/teensy_code/lib/HexapodController/src/position.hpp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)
- [position.hpp subtractPos](https://github.com/ManufacturedMotion/Hexapod/blob/main/mk2/code/real_time/teensy_code/lib/HexapodController/src/position.hpp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)
- [position.hpp distanceFromOrigin](https://github.com/ManufacturedMotion/Hexapod/blob/main/mk2/code/real_time/teensy_code/lib/HexapodController/src/position.hpp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)
- [three_by_matrices.hpp add](https://github.com/ManufacturedMotion/Hexapod/blob/main/mk2/code/real_time/teensy_code/lib/HexapodController/src/three_by_matrices.hpp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)

There is also this file I think we no longer need to track since we have our config.hpp with the same information
https://github.com/ManufacturedMotion/Hexapod/blob/main/mk2/code/offsets.md

@zschwid since you defined most of these functions can you give a quick look here and let me know which we will populate and which to remove? I can't remember if we discussed this in Nov and don't want to cut anything we will fill out

DillonKane, 2025-02-02:
https://github.com/ManufacturedMotion/Hexapod/pull/154

Closed 2025-02-02.

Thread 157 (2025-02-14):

Battery Voltage Measurements

Iacobacci, 2025-02-14:
- [x] Have the battery voltage stored in JSON format
- [x] Send the battery voltage to the pi every time the voltage changes a certain value
- [x] On the pi side convert the battery voltage to a percentage -> likely using a lookup table

Flow:
Teensy has the voltage divided value on a pin -> Teensy converts the divided value into a usable measure and applies noise filtering -> Teensy sends this value in a JSON blob over serial -> "Teensy" ROS node on pi is connected to UART/Serial and picks up that value -> "Teensy" Node publishes that to a topic -->  node on the Pi is listening, picks up that value, and converts it to a percentage.

DillonKane, 2025-02-20:
to fix blocking issue we can use polling counters: think of embedded course. static var for counter and increment every loop instead of using a while loop.

DillonKane, 2025-02-22:
when working on pi side we want a soft warning at 3.5V per cell and hard cutoff at 3.3V

DillonKane, 2025-02-22:
first two bullets accomplished with these updates: https://github.com/ManufacturedMotion/Hexapod/pull/178

DillonKane, 2025-04-17:
lithium ion open cell voltage

Closed 2025-06-29.

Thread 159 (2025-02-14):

JSON Parsing for 18 Leg Position Setting

Iacobacci, 2025-02-14:
G2 code change in main.cpp

JSON Parsing for 18 Leg Position Setting -- Would need to use Arduino JSON Parsing

This command would always send a key value pair for ALL 18 motors. It can call move to pos at speed underneath to do actual movements

```
{
    "L0S1": 0,
    ...
    "L5S3": -3.14
}
```

DillonKane, 2025-02-16:
example command:

```
G2 {"L0S1":0,"L0S2":0,"L0S3":0,"L1S1":0,"L1S2":0,"L1S3":0,"L2S1":0,"L2S2":0,"L2S3":0,"L3S1":0,"L3S2":0,"L3S3":0,"L4S1":0,"L4S2":0,"L4S3":0,"L5S1":0,"L5S2":0,"L5S3":0}
```

DillonKane, 2025-02-16:
https://github.com/ManufacturedMotion/Hexapod/pull/166

Closed 2025-02-20.

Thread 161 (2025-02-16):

- not sure if i want to do this or send unique val for no measure

DillonKane, 2025-02-16:
```
        //todo - not sure if i want to do this or send unique val for no measure
```

In file mk2/code/real_time/teensy_code/lib/HexapodController/src/voltage_monitor.cpp
undefined

DillonKane, 2025-02-16:
accidentally made this from inside vscode

Closed 2025-02-16.

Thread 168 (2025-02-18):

Containerized LEDs

Iacobacci, 2025-02-18:
Setup the LEDs to work within the docker container, rather than requiring additional configuration at startup. There may still be some configuration required to get the LEDs accessible to the docker container, but all the python packages installations should be handled by the container. (python-requirements.txt)

Iacobacci, 2025-03-04:
#188 Since there was functionality missing (joystick) in #187

Closed 2025-03-04.

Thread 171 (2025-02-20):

Strafing Twist -> Walk Setup Functions

Iacobacci, 2025-02-20:
Create a new package `gait` + node `teensy_gait` that takes in twist strafe values and converts it to the hexapod.walk_setup on the teensy.

- Subscribe to the /cmd_vel topic
- Convert this to the format needed for the teensy gait
- Publish the formatted command to the /to_teensy topic

Right Stick X-Axis: Linear +/- X (Holonomic Mode (Strafing) -- Walking in a direction without turning in that direction)
Right Stick Y-Axis: Linear +/- Y (Holonomic Mode (Strafing) -- Walking in a direction without turning in that direction)

Reference (but do better): mk2/code/non_real_time/container/src/ros2_ws/src/gait_node/gait_node/gait.py --  note: this is untested and may not work.

Existing Teensy Node (requires rework): https://github.com/ManufacturedMotion/Hexapod/blob/main/mk2/code/non_real_time/container/src/ros2_ws/src/teensy_node/teensy_node/uart_teensy.py

Change these:

```
 self.publisher_ = self.create_publisher(String, '/teensy_receive', 10)
 self.subscriber = self.create_subscription(String,'teensy_send',self.send_to_teensy,10)
```

```
 self.publisher_ = self.create_publisher(String, '/from_teensy', 10)
 self.subscriber = self.create_subscription(String,'/to_teensy',self.send_to_teensy,10)
```

DillonKane, 2025-02-27:
```
ros2 run teensy_node teensy_node

ros2 run gait teensy_gait
```

DillonKane, 2025-03-02:
https://github.com/ManufacturedMotion/Hexapod/pull/186

Closed 2025-03-02.

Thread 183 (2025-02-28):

Teensy gait account for yaw

zschwid, 2025-02-28:
- [ ] Add new (optional) argument to walkSetup called yaw to indicate the yaw that should be completed during the walk
- [ ] Update gait to account for changes in Yaw

DillonKane, 2025-03-01:
I think we also want walk setup to account for roll/pitch. Right now they are not consumed

zschwid, 2025-04-17:
Roll and pitch require no steps so will be handled by linearMove, which is already in place.

zschwid, 2025-04-17:
May change all walkSetup commands to linearMoveSetup commands instead which would account for all 6 axis motion with steps

zschwid, 2025-05-05:
In progress, troubleshooting returning to neutral.

Closed 2025-05-17.

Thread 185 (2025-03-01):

Add button mapping for Speed to teensy gait

DillonKane, 2025-03-01:

DillonKane, 2025-03-07:
send speed as part of MV json. speed will scale with how far joystick is pushed. Can also then tweak step size in gait node to walk with larger steps.

faster speed will prevent queue build up

Closed 2025-03-08.

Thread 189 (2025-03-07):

Option to power down all servos

DillonKane, 2025-03-07:

DillonKane, 2025-03-07:
maybe make this what the y button does and we can remove starfish?

zschwid, 2025-05-17:
Complicated to do with Teensy compatible PWMServo library, not worth the effort / time commitment at this point in development cycle

Closed 2025-05-17.

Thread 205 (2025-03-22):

new json/gcode command

DillonKane, 2025-03-22:
"TUNE" key for json

add option to tune only one motor at a time by providing the leg, motor and position

DillonKane, 2025-03-22:
make sure to also add instruction to wiki page

DillonKane, 2025-03-23:
https://github.com/ManufacturedMotion/Hexapod/pull/213

Closed 2025-03-23.

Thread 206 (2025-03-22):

parsing safety nets

DillonKane, 2025-03-22:
ex:
```
        else if (token[0] == 'L') {
            uint8_t L_end = token.find('S');
            uint8_t leg = std::stoi(token.substr(1, L_end - 1));
            uint8_t axis = std::stoi(token.substr(L_end + 1, 1)) - 1;
            double pos = std::stod(token.substr(L_end + 2));
            if ((leg >= 0 && leg < NUM_LEGS) && (axis >= 0 && axis < NUM_AXES_PER_LEG)) {
                _leg_positions[leg][axis] = pos;
            }
        }
```
should not move motors when given L3 0 0 0 command

probably just return if S is missing from key
```
    if (L_end == std::string::npos) {
        return;  // or use 'continue;' if this is inside a loop
    }
```

DillonKane, 2025-03-23:
https://github.com/ManufacturedMotion/Hexapod/pull/213

Closed 2025-03-23.

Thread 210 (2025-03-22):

move images/cad/pcb/etc. to another spot?

DillonKane, 2025-03-22:
should we move the cad, pcbs, images, etc. (pretty much anything that is not code) to another location? We don't need access to these files on the pi or teensy. Any time these files are touched it slows down the git pull process for me and it will consume extra memory on the pi.

Maybe instead of moving everything else, we can move Mk1 / Mk2 into submodules? Then on the pi we only need to clone the submodule and not the full repo?

DillonKane, 2025-03-22:
I am thinking of some submodule options:
* `mk1/code`, `mk2/code`
  * would have teensy and pi code in same repo
* `mk1/code/non_real_time`, `mk2/code/non_real_time`
  * would only have pi code
* `mk1/code/real_time`, `mk2/code/rreal_time`
  * would only have teensy code
* or a combination of above:   `mk1/code/real_time`, `mk2/code/rreal_time`, & `mk1/code/non_real_time`, `mk2/code/non_real_time`
  * user can clone non_real_time on pi for remote dev and minimal overhead. Can also clone teensy code to a separate space for teensy dev with no extra overhead

Closed 2025-05-27.

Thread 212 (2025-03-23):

change DEBUG to DEBUG_LEVEL

DillonKane, 2025-03-23:
instead of 1 or 0 give more levels for debug printing

i.e.
0 - no debug
1 - print serial msgs
2 - print leg movement calculations, etc.

DillonKane, 2025-03-23:
make serial class with function that take msg and min log level.

ex: <class function>.log(<msg>, 3)
only logs the message if the DEBUG_LEVEL >= 3 in user_config

zschwid, 2025-04-13:
Use preprocessor to handle debug levels so that debug commands not in use get compiled out

DillonKane, 2025-04-22:
WIP: https://github.com/ManufacturedMotion/Hexapod/tree/serial_logging

I have most of the logging handled by the preprocessor on above branch but hit a snag. The current parser code for json/gcode/serial commands requires a pointer to our hexapod instance to be passed around. The only alternative to this I am thinking of now is to have the code to execute json/gcode commands live inside of Hexapod.cpp. I don't really like this though, I want to try and keep the parsing in separate source files

DillonKane, 2025-04-25:
remove serialHandler and just use serial.print

kill gcode support!!

DillonKane, 2025-05-04:
https://github.com/ManufacturedMotion/Hexapod/pull/231

Closed 2025-05-04.

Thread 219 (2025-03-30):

Teensy use and publish toe limit switch state changes to RPi

zschwid, 2025-03-30:
First pass: publish the toe limit switch state changes up to RPi

Iacobacci, 2025-07-17:
We removed the limit switches from the current design, so closing out this issue as not planned

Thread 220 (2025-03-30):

Teensy use toe limit switch states in gait

zschwid, 2025-03-30:
Instead of lifting and putting legs down a static amount, utilize the toe limit switches to dynamically adjust how far legs are put down during a step.

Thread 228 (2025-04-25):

reorganize library folder

DillonKane, 2025-04-25:

DillonKane, 2025-04-25:
when doing this we can pull things out of the hexapod class where necessary. I.E. voltage sensor does not need an instance in hexapod.cpp

in main.cpp
hexapod.voltageSensor.checkVoltage()  ->  voltageSensor.checkVoltage()

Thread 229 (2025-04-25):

All hexapod movements to return move time

DillonKane, 2025-04-25:
Zack to update hexapod.cpp so all movements return a time

Dillon to update serial comms after so Pi gets knowledge of times. use this for command timing spacing

DillonKane, 2025-05-05:
enqueRapidMove and WalkSetup return the times. send these back to the pi to be used for delay before next send

DillonKane, 2025-05-07:
```
[teensy_node-3] [INFO] [1746579720.404851495] [teensy_node]: TeensyNode received {"MOVE_TIME":416} from teensy
[teensy_node-3] [INFO] [1746579923.193385088] [teensy_node]: TeensyNode writing to teensy serial: {"MV": "WLK", "X": 45.097, "Y": -145.391, "Z": 0, "ROLL": 0.0, "PTCH": 0.0, "YAW": 0.0, "SPD": 270.0}
[teensy_node-3] [INFO] [1746579924.204767718] [teensy_node]: TeensyNode received {"MOVE_TIME":562} from teensy
[teensy_node-3] [INFO] [1746579924.393246604] [teensy_node]: TeensyNode writing to teensy serial: {"MV": "WLK", "X": -93.253, "Y": -155.737, "Z": 0, "ROLL": 0.0, "PTCH": 0.0, "YAW": 0.0, "SPD": 286.73}
[teensy_node-3] [INFO] [1746579925.404693853] [teensy_node]: TeensyNode received {"MOVE_TIME":632} from teensy
[teensy_node-3] [INFO] [1746579925.593209793] [teensy_node]: TeensyNode writing to teensy serial: {"MV": "WLK", "X": -96.24, "Y": 156.152, "Z": 0, "ROLL": 0.0, "PTCH": 0.0, "YAW": 0.0, "SPD": 288.19}
[teensy_node-3] [INFO] [1746579926.604831088] [teensy_node]: TeensyNode received {"MOVE_TIME":1729} from teensy
[teensy_node-3] [INFO] [1746579926.793208748] [teensy_node]: TeensyNode writing to teensy serial: {"MV": "WLK", "X": 5.326, "Y": 136.0, "Z": 0, "ROLL": 0.0, "PTCH": 0.0, "YAW": 0.0, "SPD": 264.21}
[teensy_node-3] [INFO] [1746579927.804765532] [teensy_node]: TeensyNode received {"MOVE_TIME":514} from teensy
[teensy_node-3] [INFO] [1746579927.993193690] [teensy_node]: TeensyNode writing to teensy serial: {"MV": "WLK", "X": 3.993, "Y": 54.663, "Z": 0, "ROLL": 0.0, "PTCH": 0.0, "YAW": 0.0, "SPD": 250}
[teensy_node-3] [INFO] [1746579929.004733462] [teensy_node]: TeensyNode received {"MOVE_TIME":219} from teensy
[teensy_node-3] [INFO] [1746579929.193196099] [teensy_node]: TeensyNode writing to teensy serial: {"MV": "WLK", "X": 88.314, "Y": 0.0, "Z": 0, "ROLL": 0.0, "PTCH": 0.0, "YAW": 0.0, "SPD": 250}
[teensy_node-3] [INFO] [1746579930.204819695] [teensy_node]: TeensyNode received {"MOVE_TIME":352} from teensy
[teensy_node-3] [INFO] [1746579930.393195681] [teensy_node]: TeensyNode writing to teensy serial: {"MV": "WLK", "X": 72.372, "Y": 0.0, "Z": 0, "ROLL": 0.0, "PTCH": 0.0, "YAW": 0.0, "SPD": 250}
[teensy_node-3] [INFO] [1746579931.404801247] [teensy_node]: TeensyNode received {"MOVE_TIME":289} from teensy
[teensy_node-3] [INFO] [1746579931.593315696] [teensy_node]: TeensyNode writing to teensy serial: {"MV": "WLK", "X": 0.0, "Y": -31.302, "Z": 0, "ROLL": 0.0, "PTCH": 0.0, "YAW": 0.0, "SPD": 250}
[teensy_node-3] [INFO] [1746579932.604832306] [teensy_node]: TeensyNode received {"MOVE_TIME":125} from teensy
[teensy_node-3] [INFO] [1746579933.593194917] [teensy_node]: TeensyNode writing to teensy serial: {"MV": "WLK", "X": 0.0, "Y": -180.031, "Z": 0, "ROLL": 0.0, "PTCH": 0.0, "YAW": 0.0, "SPD": 285.62}
[teensy_node-3] [INFO] [1746579934.604872788] [teensy_node]: TeensyNode received {"MOVE_TIME":629} from teensy
[teensy_node-3] [INFO] [1746579934.793219564] [teensy_node]: TeensyNode writing to teensy serial: {"MV": "WLK", "X": -176.0, "Y": 47.375, "Z": 0, "ROLL": 0.0, "PTCH": 0.0, "YAW": 0.0, "SPD": 287.29}
[teensy_node-3] [INFO] [1746579935.804824257] [teensy_node]: TeensyNode received {"MOVE_TIME":633} from teensy
[teensy_node-3] [INFO] [1746579935.993250587] [teensy_node]: TeensyNode writing to teensy serial: {"MV": "WLK", "X": 97.243, "Y": 152.188, "Z": 0, "ROLL": 0.0, "PTCH": 0.0, "YAW": 0.0, "SPD": 286.04}
[teensy_node-3] [INFO] [1746579937.004038354] [teensy_node]: TeensyNode received {"MOVE_TIME":1701} from teensy
[teensy_node-3] [INFO] [1746579946.193343317] [teensy_node]: TeensyNode writing to teensy serial: {"MV": "WLK", "X": 132.329, "Y": -60.921, "Z": 0, "ROLL": 0.0, "PTCH": 0.0, "YAW": 0.0, "SPD": 267.42}
[teensy_node-3] [INFO] [1746579947.204978353] [teensy_node]: TeensyNode received {"MOVE_TIME":1750} from teensy
[teensy_node-3] [INFO] [1746579947.393282625] [teensy_node]: TeensyNode writing to teensy serial: {"MV": "WLK", "X": 32.563, "Y": 0.0, "Z": 0, "ROLL": 0.0, "PTCH": 0.0, "YAW": 0.0, "SPD": 250}
[teensy_node-3] [INFO] [1746579948.404808428] [teensy_node]: TeensyNode received {"MOVE_TIME":130} from teensy
[teensy_node-3] [INFO] [1746579958.793256351] [teensy_node]: TeensyNode writing to teensy serial: {"MV": "WLK", "X": -101.07, "Y": -19.746, "Z": 0, "ROLL": 0.0, "PTCH": 0.0, "YAW": 0.0, "SPD": 256.84}
[teensy_node-3] [INFO] [1746579959.804694887] [teensy_node]: TeensyNode received {"MOVE_TIME":400} from teensy
[teensy_node-3] [INFO] [1746579959.993268568] [teensy_node]: TeensyNode writing to teensy serial: {"MV": "WLK", "X": -156.0, "Y": -39.031, "Z": 0, "ROLL": 0.0, "PTCH": 0.0, "YAW": 0.0, "SPD": 273.93}
[teensy_node-3] [INFO] [1746579961.005039375] [teensy_node]: TeensyNode received {"MOVE_TIME":586} from teensy
[teensy_node-3] [INFO] [1746579961.193264179] [teensy_node]: TeensyNode writing to teensy serial: {"MV": "WLK", "X": -152.0, "Y": 37.853, "Z": 0, "ROLL": 0.0, "PTCH": 0.0, "YAW": 0.0, "SPD": 271.94}
[teensy_node-3] [INFO] [1746579962.204649583] [teensy_node]: TeensyNode received {"MOVE_TIME":575} from teensy
[teensy_node-3] [INFO] [1746579962.393244278] [teensy_node]: TeensyNode writing to teensy serial: {"MV": "WLK", "X": -124.0, "Y": 25.087, "Z": 0, "ROLL": 0.0, "PTCH": 0.0, "YAW": 0.0, "SPD": 261.56}
[teensy_node-3] [INFO] [1746579963.404000685] [teensy_node]: TeensyNode received {"MOVE_TIME":483} from teensy
[teensy_node-3] [INFO] [1746579963.593193791] [teensy_node]: TeensyNode writing to teensy serial: {"MV": "WLK", "X": -39.079, "Y": 6.806, "Z": 0, "ROLL": 0.0, "PTCH": 0.0, "YAW": 0.0, "SPD": 250}
```

seeing suspicious times reported occassionally

Closed 2025-06-23.

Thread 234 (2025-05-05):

fix new serial bug

DillonKane, 2025-05-05:
something is sending a bunch of empty commands, or causing the teensy to report receiving empty commands, even when log level  = 0

DillonKane, 2025-05-07:
https://github.com/ManufacturedMotion/Hexapod/pull/237

Closed 2025-05-07.

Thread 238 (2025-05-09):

Reinforce S3

Iacobacci, 2025-05-09:
Reinforce the S3 breaking points by increasing the amount of material around the S2 connector.

Closed 2025-05-21.

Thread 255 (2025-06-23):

New LED Mount

Iacobacci, 2025-06-23:
@zschwid Designed a new hexapod mount, @Iacobacci drop it into the current files and upload

Closed 2025-06-28.

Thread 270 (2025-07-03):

Test New Breakout PCBs

DillonKane, 2025-07-03:

DillonKane, 2025-07-17:
good to have but don't fix gobilda issues. 6x new breakouts will blow the 30A fuse, so only attach a limited number

Closed 2025-07-17.

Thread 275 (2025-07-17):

Increase Lid Screen Clearance

Iacobacci, 2025-07-17:
Currently the lid prevents access to the top and side of the screen, preventing scrolling from working. Increase the chamfer clearance around the screen.

Iacobacci, 2025-08-26:
Closing this out as it will be tackled in the full leg redesign.

Closed 2025-08-26.

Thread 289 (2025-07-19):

Add Protection Diodes

Iacobacci, 2025-07-19:
- Add protection diodes to the PCB to prevent back powering from moving the legs.
- Add protection diode to prevent back powering the board from a flipped battery connection

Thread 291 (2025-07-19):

Reduce Leg/Hexapod Printed Volume

Iacobacci, 2025-07-19:
The legs and Hexapod could be made lighter and allow for better airflow if the 3D prints were better optimized.

Iacobacci, 2025-09-01:
Closing as this will be covered with the leg redesign

Closed 2025-09-01.

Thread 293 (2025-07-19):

[CAD] Easily Replaceable Servos

Iacobacci, 2025-07-19:
Servos should be replaceable without needing to fully disassemble each leg.

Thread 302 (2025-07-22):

Servo Selection

Iacobacci, 2025-07-22:
The current servo choice results in servos either burning out or overheating.

Requirements:
- <$40 per servo ($720 for all 18 servos)
- Does not over hear (preferably metal body so we can increase air flow)
- >20KG minimum. Ideally in the 30KG range

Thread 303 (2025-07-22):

80mm Fan -> 2 40mm Fans

Iacobacci, 2025-07-22:
Modify the design to use two 40mm fans stacked horizontally, rather than one 80mm fan. The full 80mm height is not needed as we're currently blowing a lot of air at plastic, rather than focusing it on the pi.

This should result in more direct air flow, and free up space under the fan.

Closed 2025-08-12.

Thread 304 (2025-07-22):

Redesign S3

Iacobacci, 2025-07-22:
Redesign S3 with the following improvements:
- [ ] Add a Hall effect sensor w/magnet on the toe for position feedback.
- [ ] Increase the airflow around the servo.
- [ ] Better lock in the rod for the toe.
- [ ] Increase clearances so heat set inserts can be added without burning the plastic.

Iacobacci, 2025-08-26:
Closing this out as it will be tackled in the full leg redesign.

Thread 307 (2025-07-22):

Better support detaching servos

Iacobacci, 2025-07-22:
We added in support for detaching servos at OpenSauce 2025. However, not all bots will have servos that support this. To better account for that:

- [ ] Add a flag to user_config if the bot supports detaching.
- [ ] Add detach as a supported move in the queue.
- [ ] Trigger a detach every time a sit command is issued IFF the flag in user_config is set to true.

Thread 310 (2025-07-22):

Capacitors blowing fuse

Iacobacci, 2025-07-22:
Due to the inrush of current to fill up the capacitors, we are exceeding a peak current of 30A so we are blowing the main fuse. Currently, we can only add in the capacitors on 5/6 legs. This results in two different leg PCBs being needed to build the current design.

Potential solutions:
- Decrease the capacitor size per leg so all the boards are the same.
- Find a larger fuse block and confirm the board can support 35A.
- Add in transistors so we only power one leg at a time at startup.

Iacobacci, 2025-09-01:
This may be less of an issue with the switch to dc motors for S2/S3. Only S1 will be running a servo: https://github.com/ManufacturedMotion/Hex/issues/302

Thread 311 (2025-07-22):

S0 PCB Mounting

Iacobacci, 2025-07-22:
The mounting points on S0 for the PCB do not work, resulting in only one screw being used. Modify to allow the use of two screws, except on L5 where Velcro will be used instead.

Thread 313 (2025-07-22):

LED Ring Supports Right Joystick

Iacobacci, 2025-07-22:
Currently the LED ring has a mode where it will light up wherever the joystick is pointing. However, this doesn't work for the right joystick. The LED ring should light up whenever either joystick is moving, potentially having two different sets of light on at the same time

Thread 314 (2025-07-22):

Hex2 BOM Updates

Iacobacci, 2025-07-22:
The Hex2 BOM does not include:
- [ ] Springs and related parts
- [ ] GoBilda servo information

Add this information and validate current BOM is still accurate as we close out the Hex2 iteration.

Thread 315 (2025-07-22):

Hex2 CAD Updates

Iacobacci, 2025-07-22:
Clean up the assembly and publish with the following changes:

- [ ] The new springy leg
- [ ] The new(ish) version of S0

Closed 2025-08-12.

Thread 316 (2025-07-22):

S2 Pinches S3 Wire

Iacobacci, 2025-07-22:
The cross beam for S2 currently pinches the S3 wire, which resulted in it wearing down the cable sheathing around the servo wires.

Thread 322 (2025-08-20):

New s3

DillonKane, 2025-08-20:
- [x] new toe design that is more stable / does not fall out
- [x] s3 to use hall effect sensor for toe positioning

DillonKane, 2025-08-20:
new design mechanically working, just need to double check the sensor code.

also want to look into different ways of locking the sensor in place

Closed 2025-08-20.

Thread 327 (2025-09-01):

S3 CAD Revisions

Iacobacci, 2025-09-01:
- [ ] Embedded hall-effect sensor for toe position
- [ ] Better grip on hall-effect sensor
- [ ] Embedded axle coupling
- [ ] Change leg dimensions to fit within S2 redesign
- [ ] Servo -> Axle

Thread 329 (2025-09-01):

Leg PCB Redesign

Iacobacci, 2025-09-01:
- [ ] Support for 24v
- [ ] Compute on each leg
- [ ]

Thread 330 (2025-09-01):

Main PCB Redesign

Iacobacci, 2025-09-01:
- [ ] 24v -> 5v Buck Converter
- [ ] Additional pins for second fan
- [ ] Relays / Transistors for powering legs individually
- [ ] Protection Diodes (https://github.com/ManufacturedMotion/Hex/issues/289)

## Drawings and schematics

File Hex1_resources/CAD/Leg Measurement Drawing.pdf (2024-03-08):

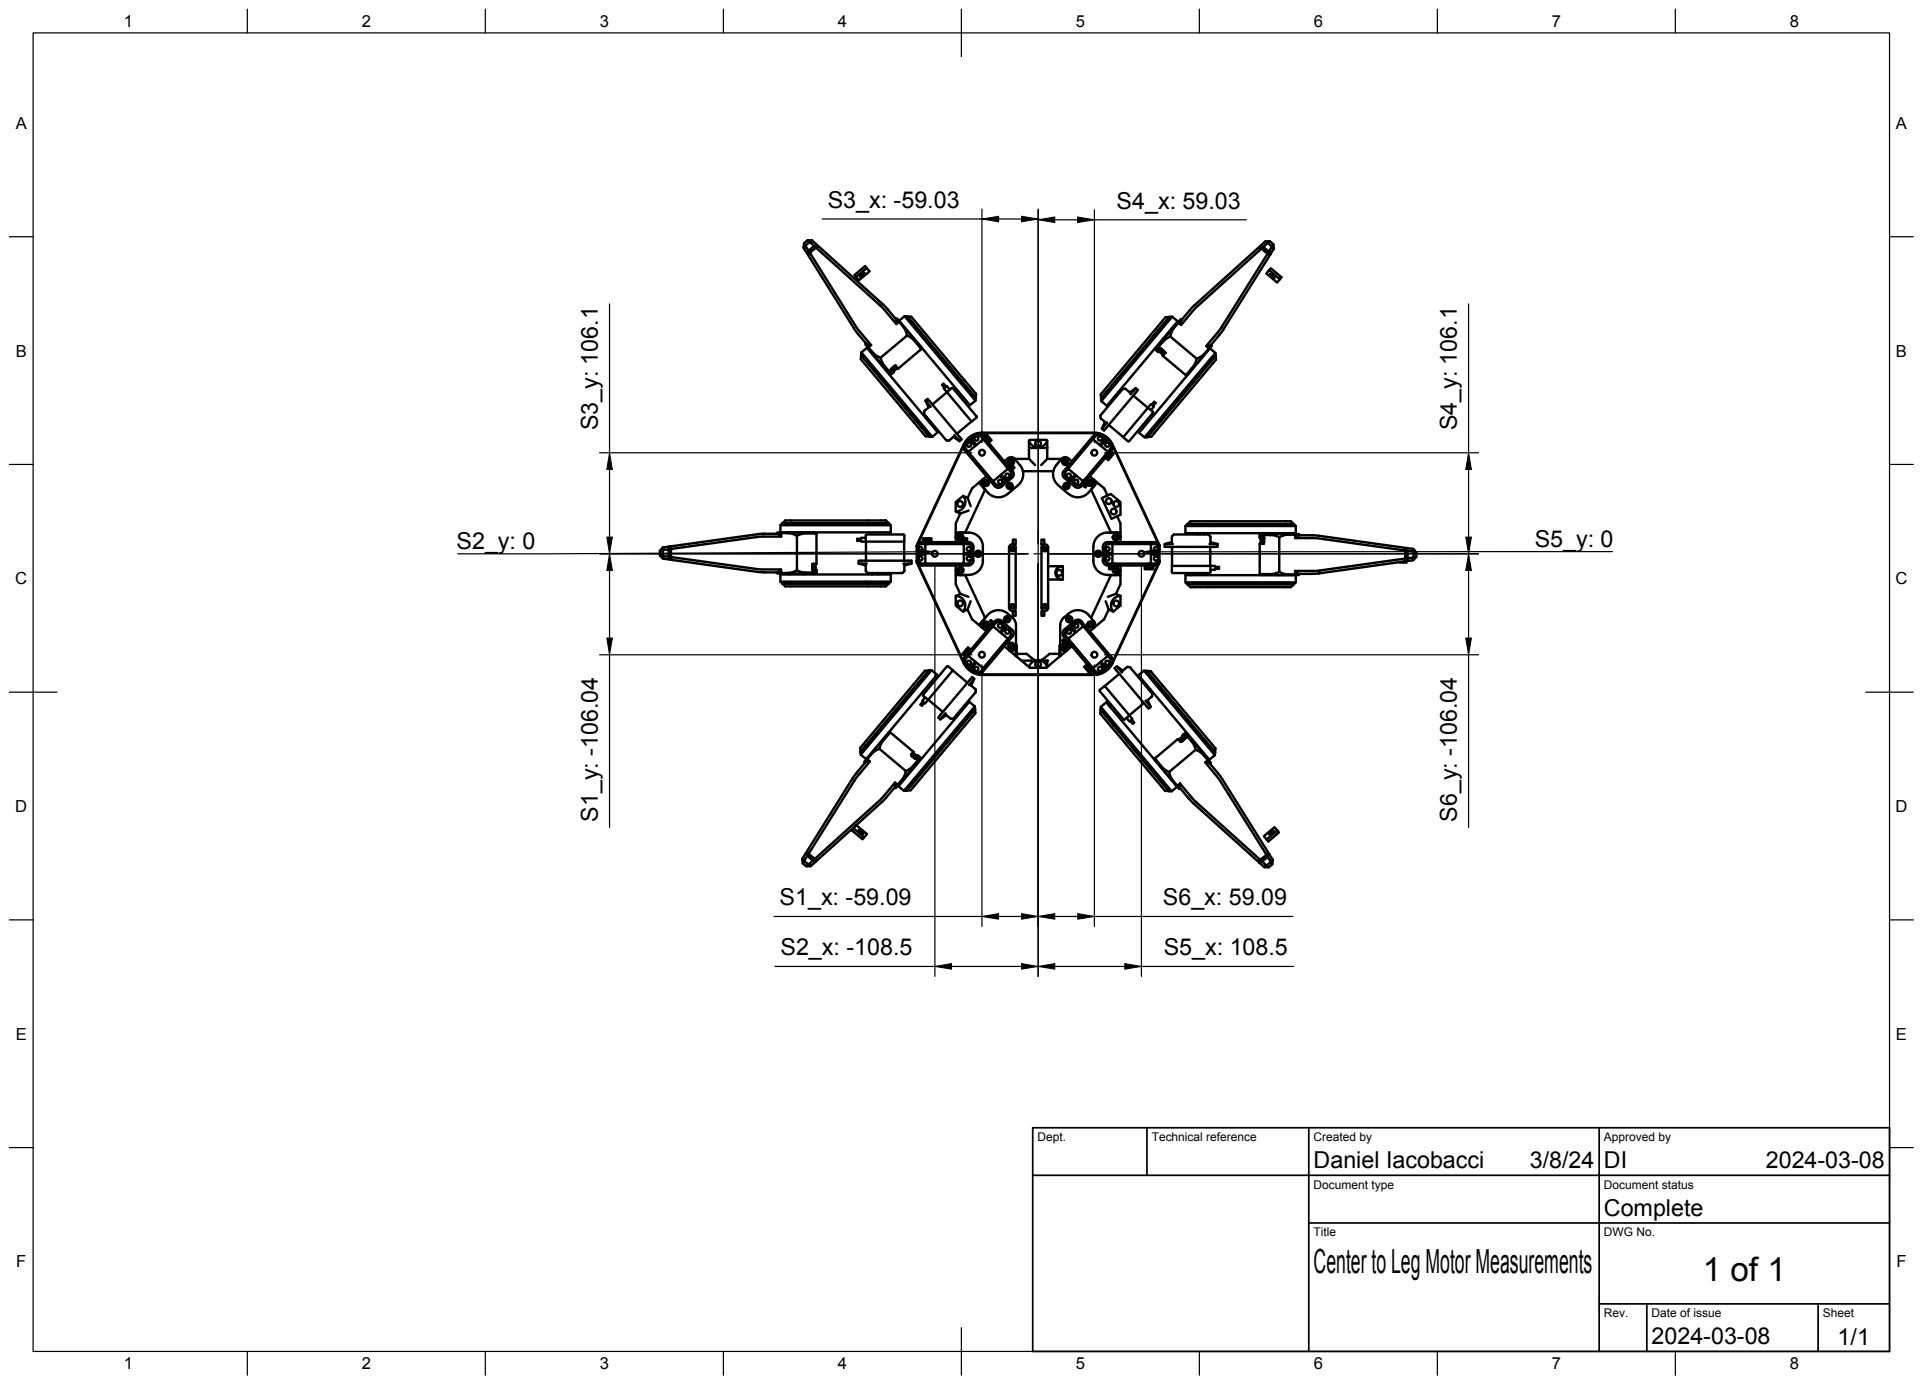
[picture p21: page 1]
Title; DWG No.; Rev.; Date of issue; Sheet; Center to Leg Motor Measurements

Dept. | Technical reference | Created by Daniel Iacobacci 3/8/24 | Approved by DI 2024-03-08

Document type | Document status Complete

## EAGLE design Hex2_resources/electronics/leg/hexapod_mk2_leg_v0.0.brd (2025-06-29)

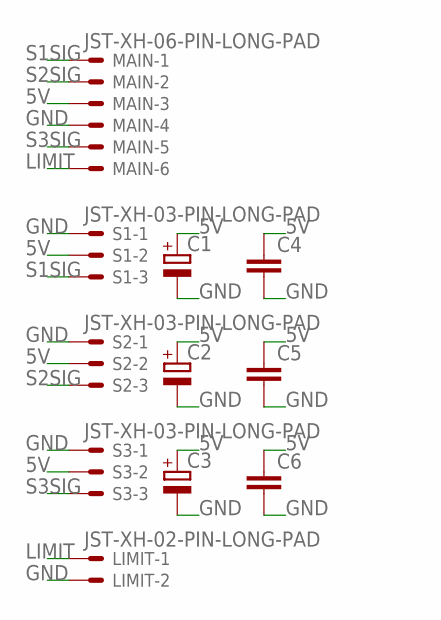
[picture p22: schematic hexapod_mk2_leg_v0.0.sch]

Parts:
C1, C2, C3: CPOL-EUE2-5; E2-5
C4, C5, C6: C-EUC1206; C1206
LIMIT: JST-XH-02-PIN-LONG-PAD; JST-XH-02-PACKAGE-LONG-PAD
MAIN: JST-XH-06-PIN-LONG-PAD; JST-XH-06-PACKAGE-LONG-PAD
S1, S2, S3: JST-XH-03-PIN-LONG-PAD; JST-XH-03-PACKAGE-LONG-PAD

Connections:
5V: C1.+, C2.+, C3.+, C4.1, C5.1, C6.1, MAIN.3, S1.2, S2.2, S3.2
GND: C1.-, C2.-, C3.-, C4.2, C5.2, C6.2, LIMIT.2, MAIN.4, S1.1, S2.1, S3.1
LIMIT: LIMIT.1, MAIN.6
S1SIG: MAIN.1, S1.3
S2SIG: MAIN.2, S2.3
S3SIG: MAIN.5, S3.3

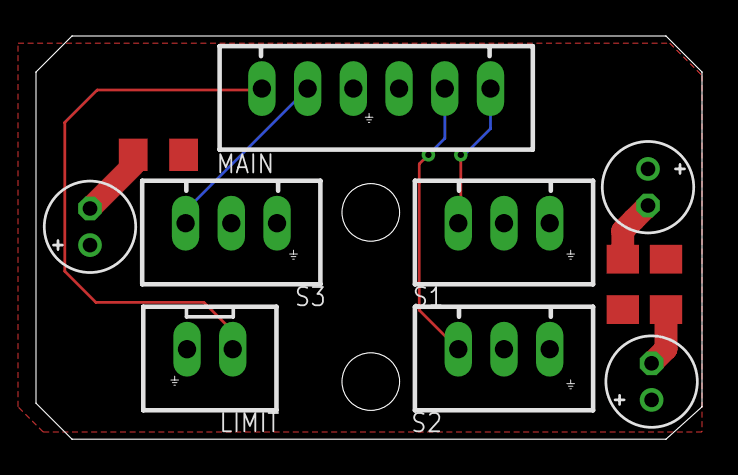
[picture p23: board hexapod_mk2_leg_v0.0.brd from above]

Board: 2 copper layers, 37.0 x 22.4 mm, 11 parts (0 on the bottom side), 6 nets.

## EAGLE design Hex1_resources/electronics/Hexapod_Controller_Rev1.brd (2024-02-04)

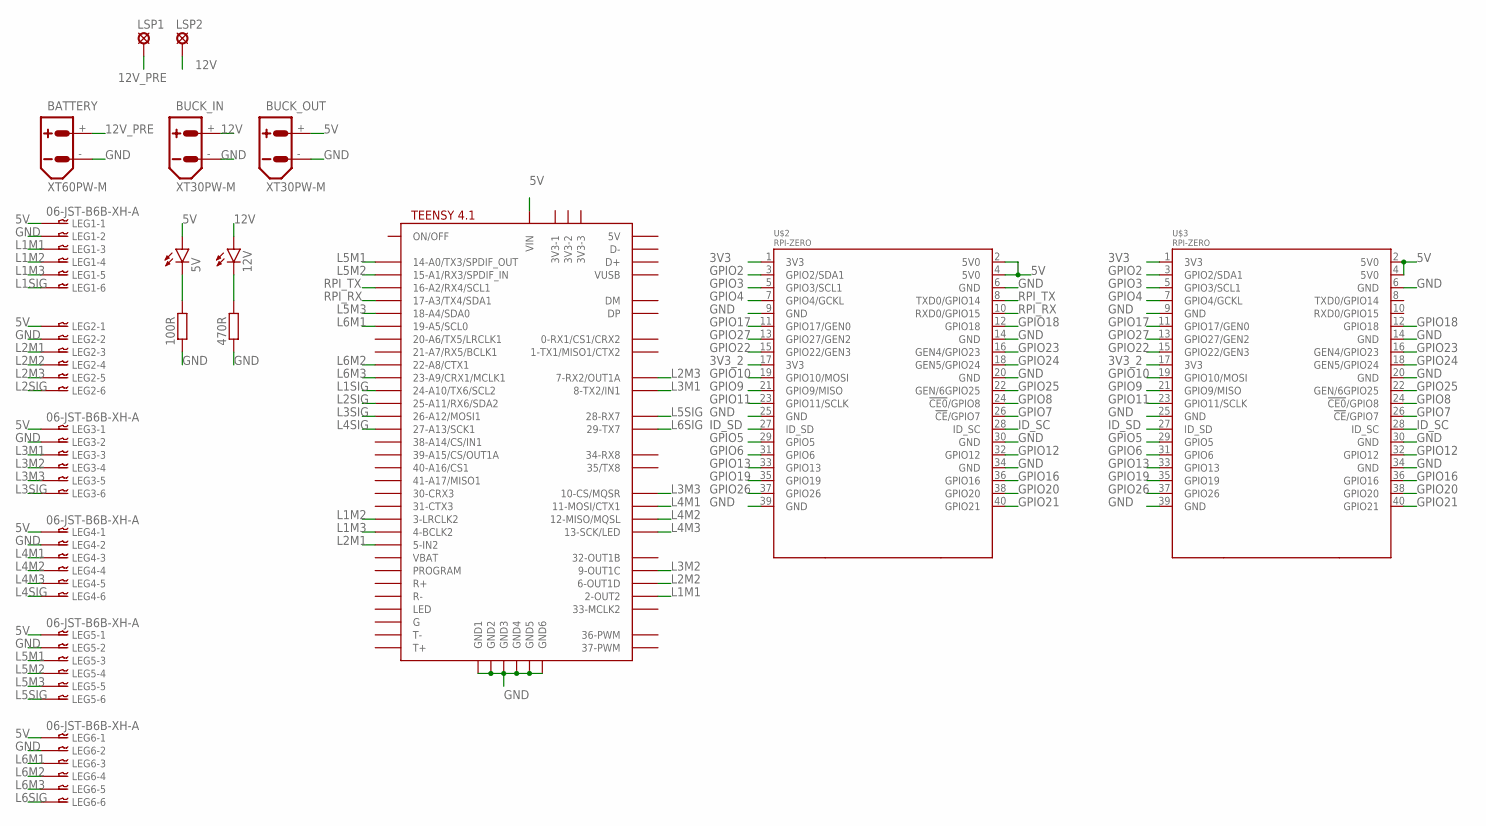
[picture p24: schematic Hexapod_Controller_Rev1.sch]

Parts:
5V, 12V: LEDCHIPLED_0805; CHIPLED_0805
100R, 470R: R-EU_R0805; R0805
BATTERY: XT60PW-M
BUCK_IN: XT30PW-M
BUCK_OUT: XT30PW-M
LEG1, LEG2, LEG3, LEG4, LEG5, LEG6: 06-JST-B6B-XH-A; B6B-XH
LSP1, LSP2: LSP10
U$1: TEENSY41
U$2, U$3: RPI-ZERO; RASPBERRYPI_BASTELSTUBE_V13_RASPI_BOARD_B+_FULL

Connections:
3V3: U$2.1 (3V3), U$3.1 (3V3)
3V3_2: U$2.17 (3V3), U$3.17 (3V3)
5V: 5V.A, BUCK_OUT.+, LEG1.P$1, LEG2.P$1, LEG3.P$1, LEG4.P$1, LEG5.P$1, LEG6.P$1, U$1.VIN, U$2.2 (5V0), U$2.4 (5V0), U$3.2 (5V0), U$3.4 (5V0)
12V: 12V.A, BUCK_IN.+, LSP2.MP
12V_PRE: BATTERY.+, LSP1.MP
GND: 100R.1, 470R.1, BATTERY.-, BUCK_IN.-, BUCK_OUT.-, LEG1.P$2, LEG2.P$2, LEG3.P$2, LEG4.P$2, LEG5.P$2, LEG6.P$2, U$1.GND1, U$1.GND2, U$1.GND3, U$1.GND4, U$1.GND5, U$1.GND6, U$2.6 (GND), U$2.9 (GND), U$2.14 (GND), U$2.20 (GND), U$2.25 (GND), U$2.30 (GND), U$2.34 (GND), U$2.39 (GND), U$3.6 (GND), U$3.9 (GND), U$3.14 (GND), U$3.20 (GND), U$3.25 (GND), U$3.30 (GND), U$3.34 (GND), U$3.39 (GND)
GPIO2: U$2.3 (GPIO2/SDA1), U$3.3 (GPIO2/SDA1)
GPIO3: U$2.5 (GPIO3/SCL1), U$3.5 (GPIO3/SCL1)
GPIO4: U$2.7 (GPIO4/GCKL), U$3.7 (GPIO4/GCKL)
GPIO5: U$2.29 (GPIO5), U$3.29 (GPIO5)
GPIO6: U$2.31 (GPIO6), U$3.31 (GPIO6)
GPIO7: U$2.26 (!CE!/GPIO7), U$3.26 (!CE!/GPIO7)
GPIO8: U$2.24 (!CE0!/GPIO8), U$3.24 (!CE0!/GPIO8)
GPIO9: U$2.21 (GPIO9/MISO), U$3.21 (GPIO9/MISO)
GPIO10: U$2.19 (GPIO10/MOSI), U$3.19 (GPIO10/MOSI)
GPIO11: U$2.23 (GPIO11/SCLK), U$3.23 (GPIO11/SCLK)
GPIO12: U$2.32 (GPIO12), U$3.32 (GPIO12)
GPIO13: U$2.33 (GPIO13), U$3.33 (GPIO13)
GPIO16: U$2.36 (GPIO16), U$3.36 (GPIO16)
GPIO17: U$2.11 (GPIO17/GEN0), U$3.11 (GPIO17/GEN0)
GPIO18: U$2.12 (GPIO18), U$3.12 (GPIO18)
GPIO19: U$2.35 (GPIO19), U$3.35 (GPIO19)
GPIO20: U$2.38 (GPIO20), U$3.38 (GPIO20)
GPIO21: U$2.40 (GPIO21), U$3.40 (GPIO21)
GPIO22: U$2.15 (GPIO22/GEN3), U$3.15 (GPIO22/GEN3)
GPIO23: U$2.16 (GEN4/GPIO23), U$3.16 (GEN4/GPIO23)
GPIO24: U$2.18 (GEN5/GPIO24), U$3.18 (GEN5/GPIO24)
GPIO25: U$2.22 (GEN/6GPIO25), U$3.22 (GEN/6GPIO25)
GPIO26: U$2.37 (GPIO26), U$3.37 (GPIO26)
GPIO27: U$2.13 (GPIO27/GEN2), U$3.13 (GPIO27/GEN2)
ID_SC: U$2.28 (ID_SC), U$3.28 (ID_SC)
ID_SD: U$2.27 (ID_SD), U$3.27 (ID_SD)
L1M1: LEG1.P$3, U$1.2-OUT2
L1M2: LEG1.P$4, U$1.3-LRCLK2
L1M3: LEG1.P$5, U$1.4-BCLK2
L1SIG: LEG1.P$6, U$1.24-A10/TX6/SCL2
L2M1: LEG2.P$3, U$1.5-IN2
L2M2: LEG2.P$4, U$1.6-OUT1D
L2M3: LEG2.P$5, U$1.7-RX2/OUT1A
L2SIG: LEG2.P$6, U$1.25-A11/RX6/SDA2
L3M1: LEG3.P$3, U$1.8-TX2/IN2 (8-TX2/IN1)
L3M2: LEG3.P$4, U$1.9-OUT1C
L3M3: LEG3.P$5, U$1.10-CS\MQSR (10-CS/MQSR)
L3SIG: LEG3.P$6, U$1.26-A12/MOSI1
L4M1: LEG4.P$3, U$1.11-MOSI/CTX1
L4M2: LEG4.P$4, U$1.12-MISO/MQSL
L4M3: LEG4.P$5, U$1.13-SCK/LED
L4SIG: LEG4.P$6, U$1.27-A13/SCK1
L5M1: LEG5.P$3, U$1.14-A0/TX3/SPDIF_OUT
L5M2: LEG5.P$4, U$1.15-A1/RX3/SPDIF_IN
L5M3: LEG5.P$5, U$1.18-A4/SDA0
L5SIG: LEG5.P$6, U$1.28-RX7
L6M1: LEG6.P$3, U$1.19-A5/SCL0
L6M2: LEG6.P$4, U$1.22-A8/CTX1
L6M3: LEG6.P$5, U$1.23-A9/CRX1/MCLK1
L6SIG: LEG6.P$6, U$1.29-TX7
unnamed: 5V.C, 100R.2
unnamed: 12V.C, 470R.2
RPI_RX: U$1.17-A3/TX4/SDA1, U$2.10 (RXD0/GPIO15)
RPI_TX: U$1.16-A2/RX4/SCL1, U$2.8 (TXD0/GPIO14)

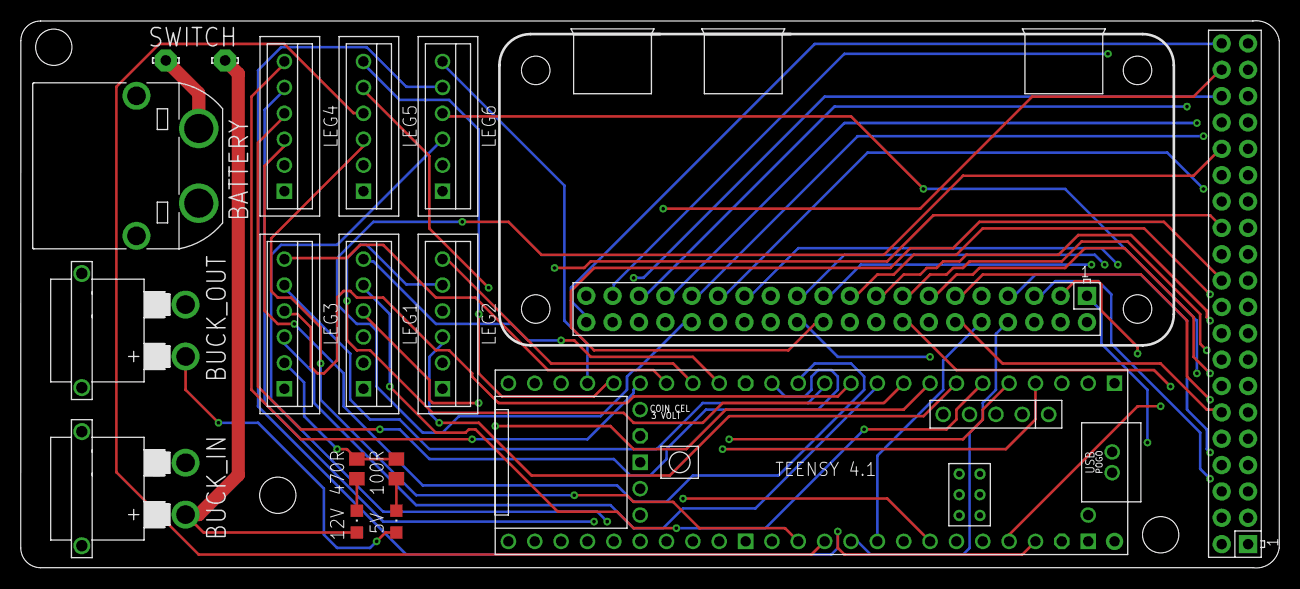
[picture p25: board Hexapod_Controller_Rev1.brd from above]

Board: 4 copper layers, 121.3 x 52.7 mm, 18 parts (0 on the bottom side), 60 nets.

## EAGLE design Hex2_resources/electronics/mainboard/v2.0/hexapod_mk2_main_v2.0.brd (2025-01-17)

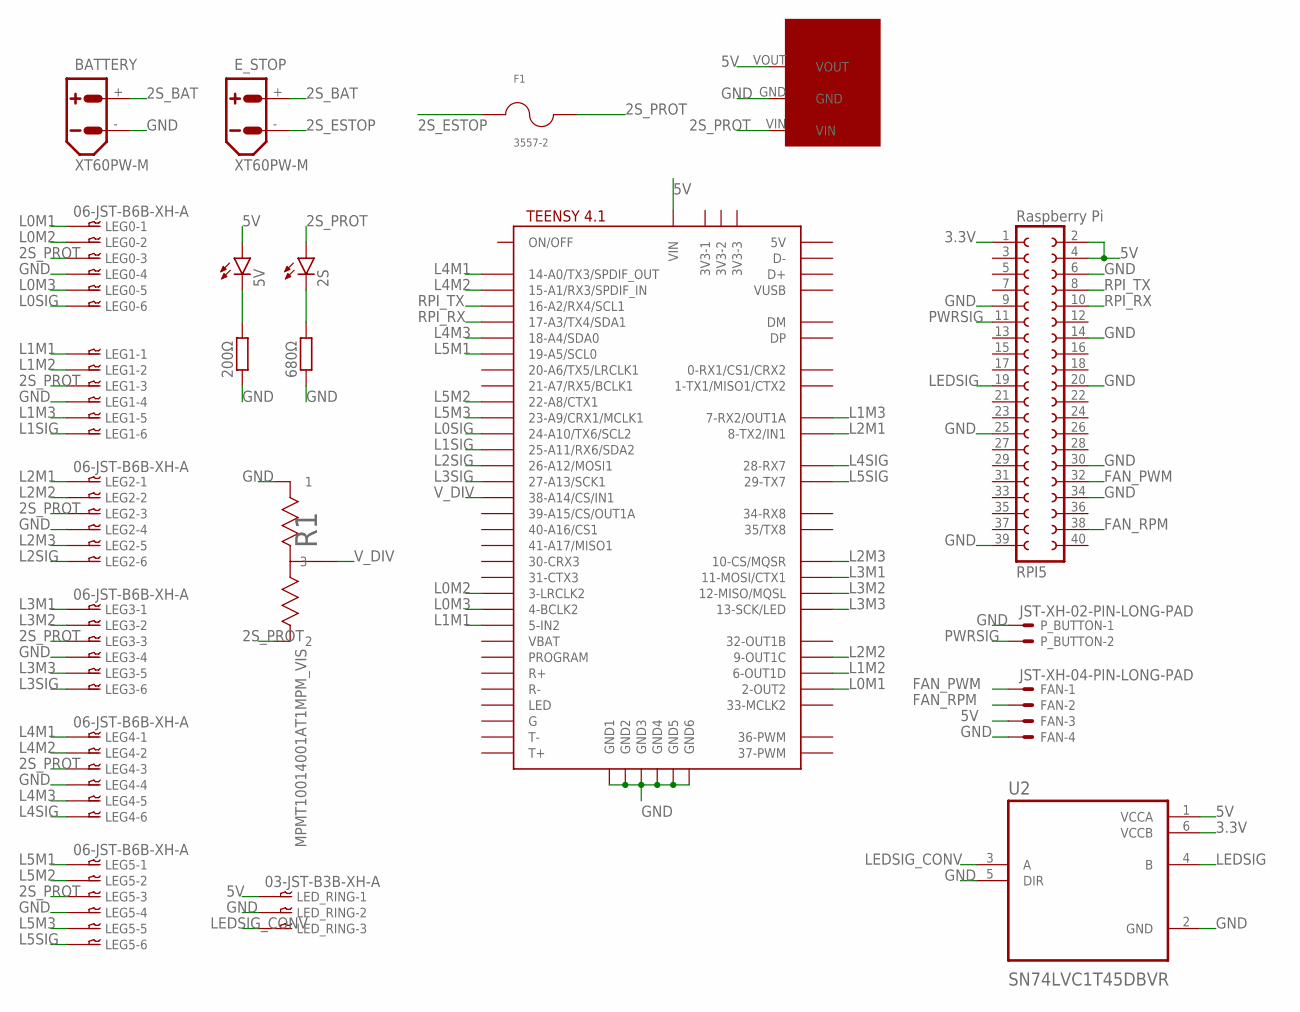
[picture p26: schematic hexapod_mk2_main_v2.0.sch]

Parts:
2S, 5V: LEDCHIPLED_0805; CHIPLED_0805
200Ω, 680Ω: R-EU_R0805; R0805
BATTERY: XT60PW-M
DFR0753: DFR0753
E_STOP: XT60PW-M
F1: 3557-2; FUSE_3557-2
FAN: JST-XH-04-PIN-LONG-PAD; JST-XH-04-PACKAGE-LONG-PAD
LED_RING: 03-JST-B3B-XH-A; B3B-XH
LEG0, LEG1, LEG2, LEG3, LEG4, LEG5: 06-JST-B6B-XH-A; B6B-XH
P_BUTTON: JST-XH-02-PIN-LONG-PAD; JST-XH-02-PACKAGE-LONG-PAD
R1: MPMT10014001AT1MPM_VIS; MPM_VIS
RPI5: Raspberry Pi; FE20-2
U2: SN74LVC1T45DBVR; SOT95P280X145-6N
U$1: TEENSY41

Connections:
2S_BAT: BATTERY.+, E_STOP.+
2S_ESTOP: E_STOP.-, F1.1_1 (1), F1.1_2 (1)
2S_PROT: 2S.A, DFR0753.VIN, F1.2_1 (2), F1.2_2 (2), LEG0.P$3, LEG1.P$3, LEG2.P$3, LEG3.P$3, LEG4.P$3, LEG5.P$3, R1.2
3.3V: RPI5.1, U2.6 (VCCB)
5V: 5V.A, DFR0753.VOUT, FAN.3, LED_RING.P$1, RPI5.2, RPI5.4, U2.1 (VCCA), U$1.VIN
FAN_PWM: FAN.1, RPI5.32
FAN_RPM: FAN.2, RPI5.38
GND: 200Ω.1, 680Ω.1, BATTERY.-, DFR0753.GND, FAN.4, LED_RING.P$2, LEG0.P$4, LEG1.P$4, LEG2.P$4, LEG3.P$4, LEG4.P$4, LEG5.P$4, P_BUTTON.1, R1.1, RPI5.6, RPI5.9, RPI5.14, RPI5.20, RPI5.25, RPI5.30, RPI5.34, RPI5.39, U2.2 (GND), U2.5 (DIR), U$1.GND1, U$1.GND2, U$1.GND3, U$1.GND4, U$1.GND5, U$1.GND6
L0M1: LEG0.P$1, U$1.2-OUT2
L0M2: LEG0.P$2, U$1.3-LRCLK2
L0M3: LEG0.P$5, U$1.4-BCLK2
L0SIG: LEG0.P$6, U$1.24-A10/TX6/SCL2
L1M1: LEG1.P$1, U$1.5-IN2
L1M2: LEG1.P$2, U$1.6-OUT1D
L1M3: LEG1.P$5, U$1.7-RX2/OUT1A
L1SIG: LEG1.P$6, U$1.25-A11/RX6/SDA2
L2M1: LEG2.P$1, U$1.8-TX2/IN2 (8-TX2/IN1)
L2M2: LEG2.P$2, U$1.9-OUT1C
L2M3: LEG2.P$5, U$1.10-CS\MQSR (10-CS/MQSR)
L2SIG: LEG2.P$6, U$1.26-A12/MOSI1
L3M1: LEG3.P$1, U$1.11-MOSI/CTX1
L3M2: LEG3.P$2, U$1.12-MISO/MQSL
L3M3: LEG3.P$5, U$1.13-SCK/LED
L3SIG: LEG3.P$6, U$1.27-A13/SCK1
L4M1: LEG4.P$1, U$1.14-A0/TX3/SPDIF_OUT
L4M2: LEG4.P$2, U$1.15-A1/RX3/SPDIF_IN
L4M3: LEG4.P$5, U$1.18-A4/SDA0
L4SIG: LEG4.P$6, U$1.28-RX7
L5M1: LEG5.P$1, U$1.19-A5/SCL0
L5M2: LEG5.P$2, U$1.22-A8/CTX1
L5M3: LEG5.P$5, U$1.23-A9/CRX1/MCLK1
L5SIG: LEG5.P$6, U$1.29-TX7
LEDSIG: RPI5.19, U2.4 (B)
LEDSIG_CONV: LED_RING.P$3, U2.3 (A)
unnamed: 5V.C, 200Ω.2
unnamed: 2S.C, 680Ω.2
PWRSIG: P_BUTTON.2, RPI5.11
RPI_RX: RPI5.10, U$1.17-A3/TX4/SDA1
RPI_TX: RPI5.8, U$1.16-A2/RX4/SCL1
V_DIV: R1.3, U$1.38-A14/CS/IN1

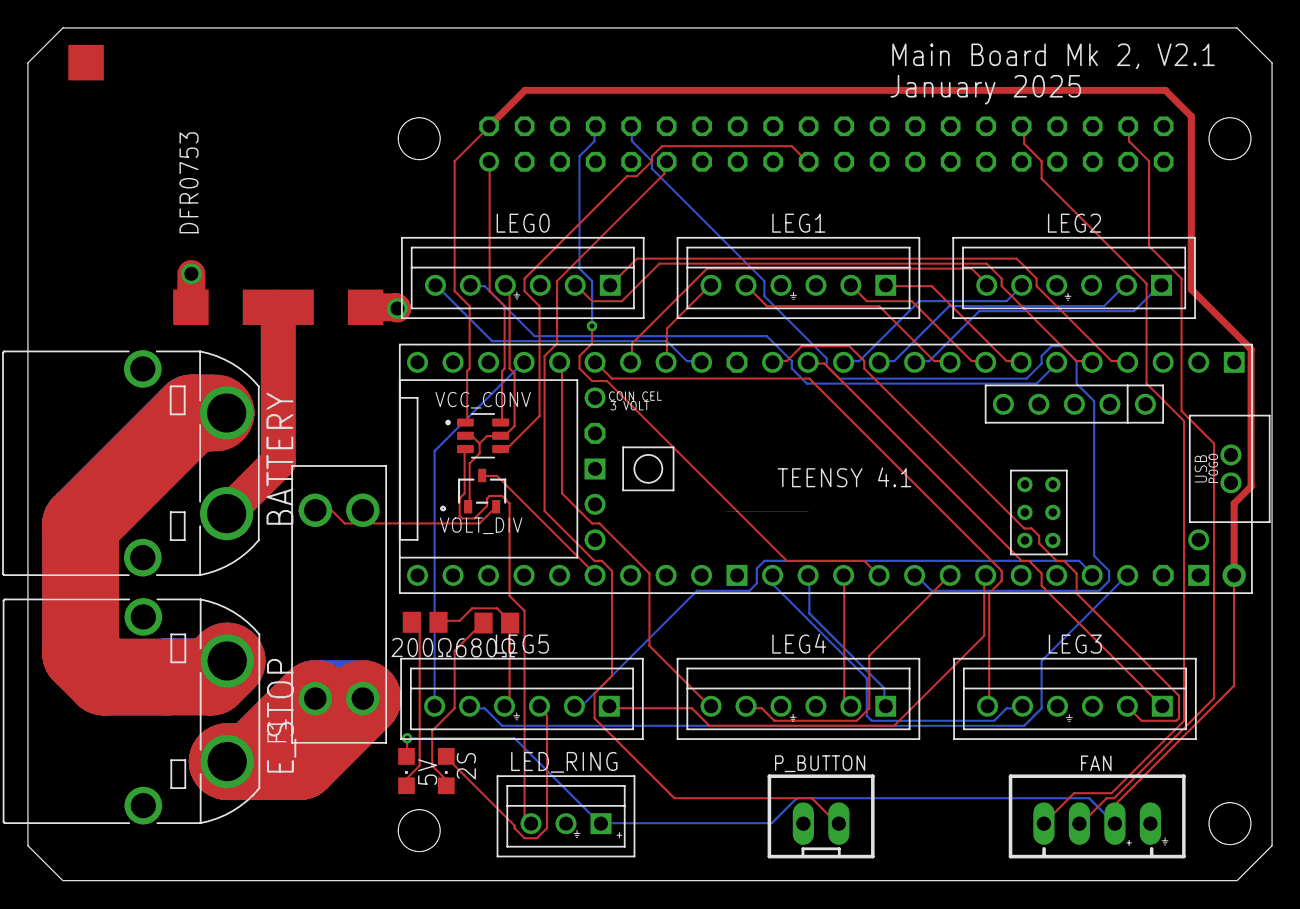
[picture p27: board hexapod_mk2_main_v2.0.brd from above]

Board: 4 copper layers, 89.0 x 61.0 mm, 21 parts (1 on the bottom side), 40 nets.

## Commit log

2023-11-12 add initial BOM
2024-02-04 Add PCB Design files
    [Hexapod_Controller_Rev1.brd, Hexapod_Controller_Rev1.sch]
2024-02-04 Update Offsets.md
    Danny's undefined motors
2024-02-04 Update Offsets.md
    Zack undefined motors
2024-02-06 add finalized 3d printed parts
    [Base_Battery Holder Final.stl, Base_Bottom Final.stl, Bearing Holder.stl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]
2024-02-06 leg and axis object compatibility
2024-02-06 Update base to fit on Bambu X1C
    [Base_Bottom Final.stl]
2024-02-12 Add updated S1 Mounts
    [L1,3,4,5 - S1 Motor Mount - Final.stl, L2 - S1 Motor Mount - Final.stl, L6 - S1 Motor Mount - Final.stl]
2024-02-14 update S1 mount
    [L1,3,4,5 - S1 Motor Mount - Final.stl]
2024-02-28 Reorganize for easer arduino dev
2024-02-28 add new 3D printed files
    [Base_Battery Holder Final.stl, Base_Bottom Final.stl, base_batteryholder_final.stl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]
2024-03-08 Add in measurements for leg motors
2024-05-17 Prepare for Mark2
    [Bearing Holder.stl, Hexapod_Controller_Rev1.brd, Hexapod_Controller_Rev1.sch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]
2024-05-25 Rename L1,3,4,5 - S1 Motor Mount - Final.stl to L2,3,4,5 - S1 Motor Mount - Final.stl
    [L2,3,4,5 - S1 Motor Mount - Final.stl]
2024-06-04 Rough draft of PCB rev 2
    [hexapod_mk2_v0.0.brd, hexapod_mk2_v0.0.sch]
2024-06-04 Draft2 of Mk2 PCB
2024-06-14 Mk1 cleanup + PCB revisions
    [Bearing Holder.stl, Hexapod_Controller_Rev1.brd, Hexapod_Controller_Rev1.sch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]
2024-06-19 Update Mk2 Schematic
    [hexapod_mk2_v0.0.brd, hexapod_mk2_v0.0.sch]
2024-06-21 Add leg breakout PCB
    [hexapod_mk2_leg_v0.0.brd, hexapod_mk2_leg_v0.0.sch, hexapod_mk2_main_v0.0.brd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]
2024-06-22 Finalized main PCB
    [hexapod_mk2_main_v0.0.brd, hexapod_mk2_main_v0.0.sch]
2024-06-22 update leg pcb
    [hexapod_mk2_leg_v0.0.brd, hexapod_mk2_leg_v0.0.sch]
2024-06-22 add board revision to pcb
    [hexapod_mk2_leg_v0.0.brd]
2024-06-23 board update
    [hexapod_mk2_main_v0.0.brd, hexapod_mk2_main_v0.0.sch]
2024-06-23 auto route main board. add silkscreens to both
    [hexapod_mk2_leg_v0.0.brd, hexapod_mk2_main_v0.0.brd]
2024-06-23 Restructure code for merger with HexpodController
    [Bearing Holder.stl, Hexapod_Controller_Rev1.brd, Hexapod_Controller_Rev1.sch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]
2024-06-23 fix autorouting issues
    [hexapod_mk2_main_v0.0.brd]
2024-06-23 fix folder structure
    [hexapod_mk2_leg_v0.0.sch]
2024-06-23 reorient main pcb label
    [hexapod_mk2_main_v0.0.brd]
2024-06-23 fix leg pcb label
    [hexapod_mk2_leg_v0.0.brd]
2024-06-23 update file hierarchy
    [Bearing Holder.stl, L2 - S1 Motor Mount - Final.stl, L2,3,4,5 - S1 Motor Mount - Final.stl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]
2024-06-24 Add PCB Gerber Files
2024-06-25 Add electronics BOM
    [electronics_bom.xlsx]
2024-06-25 take 2 at viewable BOM
2024-08-20 add draft cad
2024-08-27 add new cad assembly:
2024-09-01 puzzle piece assembly
2024-09-18 minor CAD revisions
2024-10-07 fix Dillon's motor offsets for Mk2 build
2024-11-06 CAD improvements and heatset guide
    [2024-11-05_development-hexapod-mounts.f3z]
2024-11-19 add led code
2024-11-23 Update setup.sh
    remove debug print
2024-11-24 Update mainboard schematic v1.0
    [hexapod_mk2_main_v0.0.brd, hexapod_mk2_main_v0.0.sch, hexapod_mk2_main_v1.0.brd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]
2024-11-24 fix board sever
    [hexapod_mk2_main_v1.0.brd, hexapod_mk2_main_v1.0.sch, hexapod_mk2_main_v2.0.brd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]
2024-11-25 Remove old backups for space
    [2024-11-05_development-hexapod-mounts.f3z]
2024-11-26 finalized pcb
    [hexapod_mk2_main_v2.0.sch]
2024-12-28 update CAD
    [2024-11-05_development-hexapod-mounts.f3z, 2024-12-28_development_hexapod_mounts.f3z]
2024-12-29 update Brace mounting
    [2024-12-28.2_development_hexapod_mounts.f3z]
2025-01-20 update BOM
    [hexapod_mk2_leg_v0.0.brd, hexapod_mk2_leg_v0.0.sch]
2025-01-20 update boms
    [electronics_bom.xlsx]
2025-02-01 CAD Revisions
2025-02-16 initial commit for voltage reading noise filtering
2025-02-16 use G2 to send up to 18 motor positions
2025-02-17 fix LED install
2025-02-27 new gait package & node for Twist -> json cmd. Update teensy node
2025-02-27 add X button as move to neutral pos
2025-03-01 newline when writing to teensy to avoid msg concatenation
2025-03-01 more changes to prevent msg concatenation. fine tuning of timer & step size values
2025-03-02 move LED setup to Dockerfile
2025-03-02 Switch LEDs based on button press
2025-03-03 add color changing button
2025-03-22 update LED functionality
2025-03-23 remove debug print from Danny
2025-03-24 Delete mk2/code/real_time/teensy_code/lib/HexapodController/README.md
    remove readme file
2025-04-19 move hexapod.cpp optional logging behind preprocessor. Make voltagemonitor code use new serial handler class
2025-04-21 add script for sending txt file contents to teensy
2025-05-20 Dillon gobilda servo calibration. Also add in missing file for log level definitions
2025-05-22 update led handling
2025-05-22 more LED updates
2025-06-08 add spare leg zero points
2025-06-28 fix LED reference
2025-06-29 lowpass filter
2025-06-29 servo decoupling caps
    [hexapod_mk2_leg_v0.0.brd, hexapod_mk2_leg_v0.0.sch]
2025-07-13 map dances to buttons
2025-07-14 tune GoBilda Servos
2025-07-18 fix button mapping?
2025-07-19 detach button control
2025-07-22 prep for submodule organization
    [Bearing Holder.stl, Hexapod_Controller_Rev1.brd, Hexapod_Controller_Rev1.sch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]
2025-07-23 wrap up Hex2
    [Bearing Holder.stl, Hexapod_Controller_Rev1.brd, Hexapod_Controller_Rev1.sch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]

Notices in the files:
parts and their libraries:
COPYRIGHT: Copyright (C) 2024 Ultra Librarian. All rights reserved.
